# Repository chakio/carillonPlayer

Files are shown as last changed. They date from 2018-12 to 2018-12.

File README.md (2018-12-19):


carillonPlayer
====
* arduinoで鉄琴演奏ロボット  
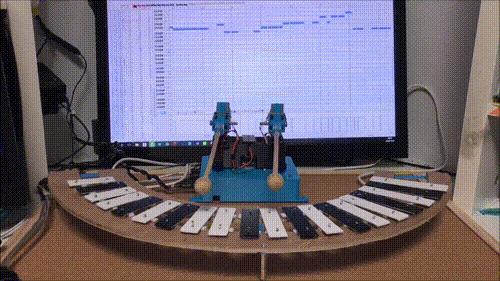
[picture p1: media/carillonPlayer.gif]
 
## Description
音データの可視化の一つとして、鉄琴演奏ロボットを作成しました。  
自作の円弧状に並ぶ鉄琴をサーボモータとソレノイドを駆使して演奏します。  
音付きの映像は[youtube](https://www.youtube.com/watch?v=UpVMlNcHM6o&feature=em-share_video_user)に公開しています。  
製作時期 2016年10月下旬〜12月初旬
## Composition
* マイコン: arduino mega
* ソレノイド: [タカハ機工株式会社 CB1037](http://www.takaha.co.jp/SHOP/cb1037.html)×2
* サーボモータ（腕,腰）:[GWSサーボ　S03T](http://akizukidenshi.com/catalog/g/gM-01794/)×3
* MIDI_Serial変換:[類似品](https://www.switch-science.com/catalog/2492/)

## Detail
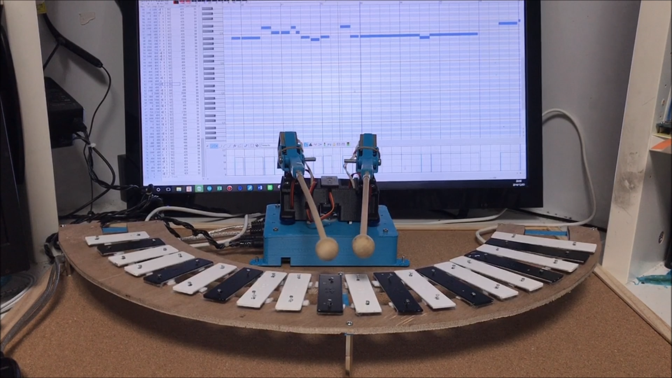
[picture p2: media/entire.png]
  

* Hardware  

鉄琴を叩く際、重要となるのは叩く際のスナップです。  
叩いた後にすぐに鉄琴からバチを離さないと、響かなくなってしまうためです。  
制作当初、すべてのアクチュエータにサーボモータを使用することを考えていました。  
しかし、プロトタイプの中で、サーボモータでスナップを効かせることは非常に困難であることがわかり、代わりのアクチュエータとしてソレノイドを採用しました。  
ソレノイドは非常に応答性がよく、一瞬だけ鉄琴を叩くという動作に適しているためです。   
以下の画像が、腕部分に着目した画像です。 

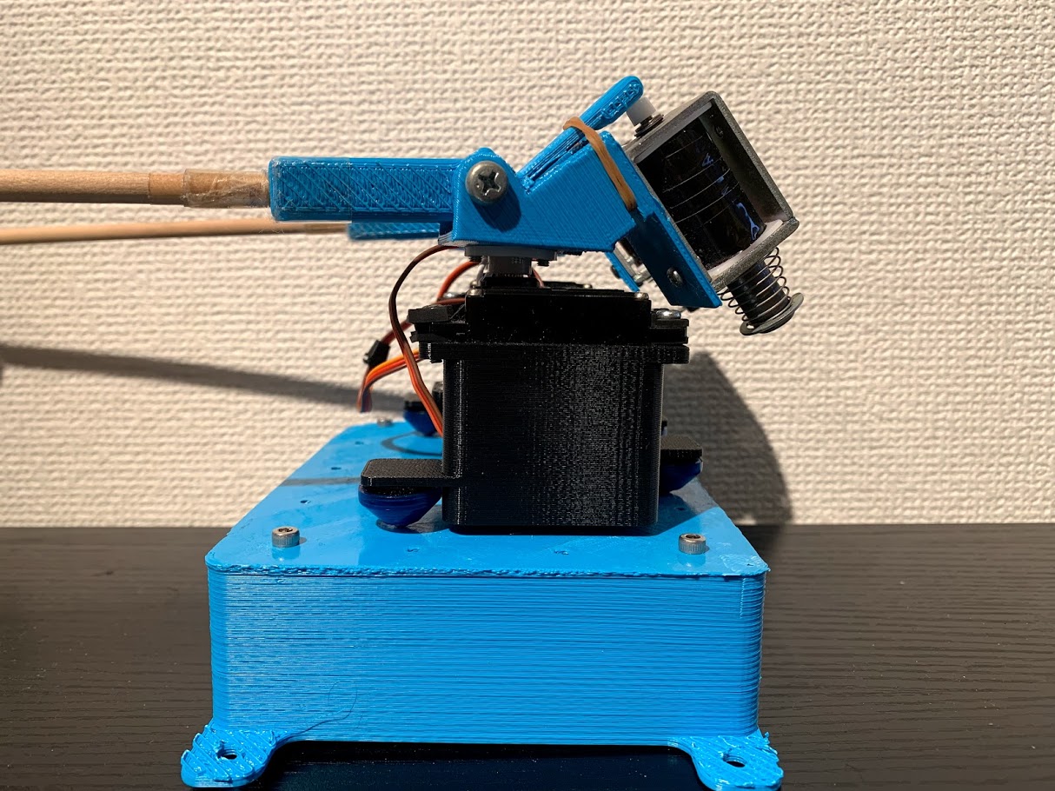
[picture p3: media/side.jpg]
  

腕部分は２つのパーツから構成されています。  
[１つ目](https://github.com/chakio/carillonPlayer/blob/master/model/solenoidHolder.stl)は、サーボモータにソレノイドを固定するパーツです。  
[２つ目](https://github.com/chakio/carillonPlayer/blob/master/model/stickHolder.stl)は、バチを把持するパーツです。  
これらを太めのネジで固定することで、ソレノイドの直動の力を回転に変換しています。  
また、一度下がったバチを元の位置に戻すために、輪ゴムを使用しています。  
このセットを２つ用意し、人と同じように双腕で演奏を行います。  
最後に、これらのパーツを[腰パーツ](https://github.com/chakio/carillonPlayer/blob/master/model/servoHolder.stl)に固定します。  

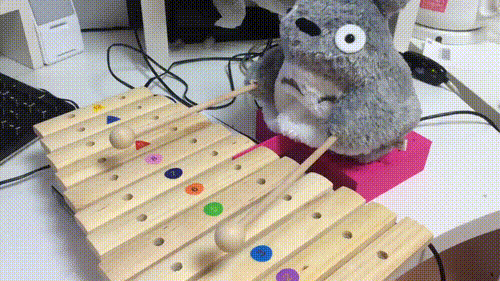
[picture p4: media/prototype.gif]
  

上記動画は、これまで説明した腕部分を使用し制作したプロトタイプのモデルです。  
小さな動きでリズミカルに叩く姿は愛らしいのですが、腕の速度に制限があり、演奏できる曲に制限がありました。  
そこで、サーボ自身を良い物に変えるのではなく、人と同様に腰部分に自由度を追加することで、遅い腕の動きを補うことを考えました。

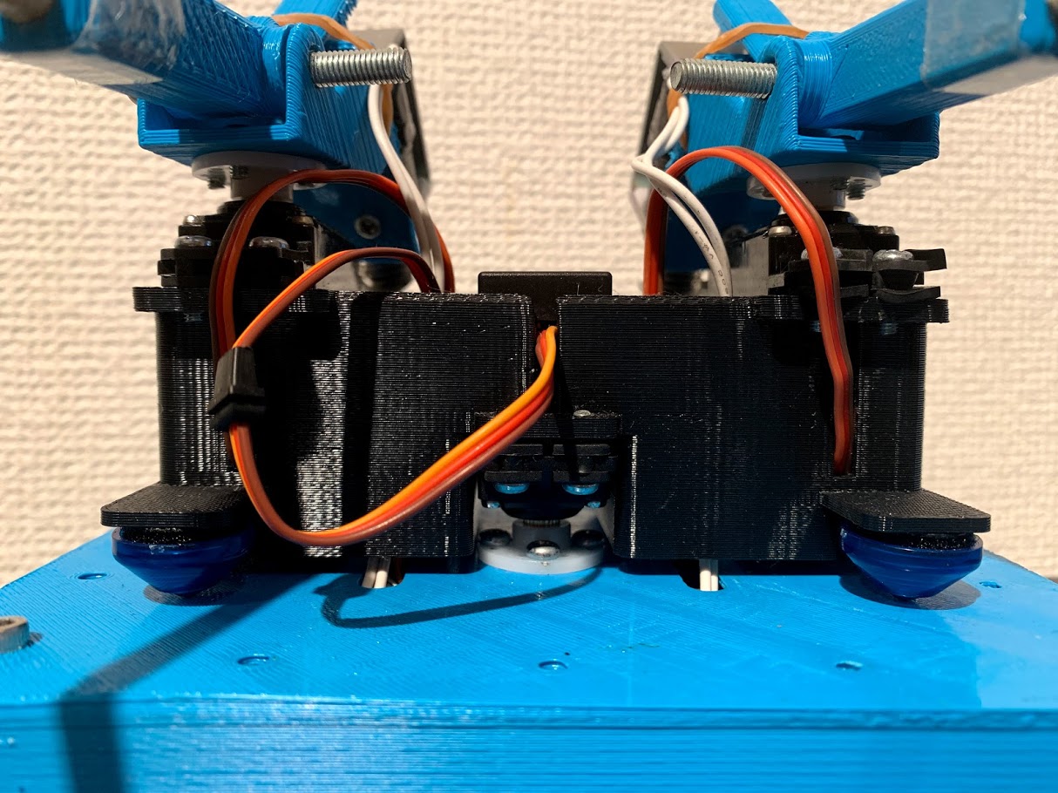
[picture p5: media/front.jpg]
  

２つの腕を固定する腰パーツに、もうひとつサーボモータを格納できるよう改良しました。   
回転をスムーズにすることと、サーボモータが痛むことを避けることを目的に４つのボールキャスターで支えるにしています。  
一番下の箱には回路などが格納されています。

* Carillon

本制作で最も苦労したのは、鉄琴周りと炒っても過言ではありません。  
まず、多くの音を演奏可能とするために、鉄琴の配置をこだわりました。  
一般的な鉄琴同様に、2列にすることを考えましたが、ハードウエアをより簡素にすることを優先し、すべての音を横に並べることを採用しました。  
更に、ロボットの可動範囲を考慮すると横一直線よりも、円弧状に配置されているほうが可動範囲をより有効活用できるため。鉄琴のプレートを円弧状に並べることとしました。  
プレートが円弧状に並ぶ鉄琴は一般的には入手できないため、入手可能な鉄琴を分解し、円弧状に再配置を行いました。  

次に、プレートの固定方法が非常に重要です。  
ただ板の上に固定するだけでは、全く音が響かなくなってしまいます。  
そこで、以下の２つの工夫を施しました。  
１つ目は、プレートをリジットな状態ではなくフローティングな状態で固定するために、プレートと板の間にフェルト生地をできるだけ細く入れています。  
接地面積が大きくなると音が響かなくなってしまいます。  
２つめは、プレートの板を一枚の板ではなく、板の内側を切り抜く加工を施しました。  
これにより、振動する空気の量がが増大し、比較的大音量かつ響くように改善されました。  

* Circuit

回路については以下の写真のとおりです。

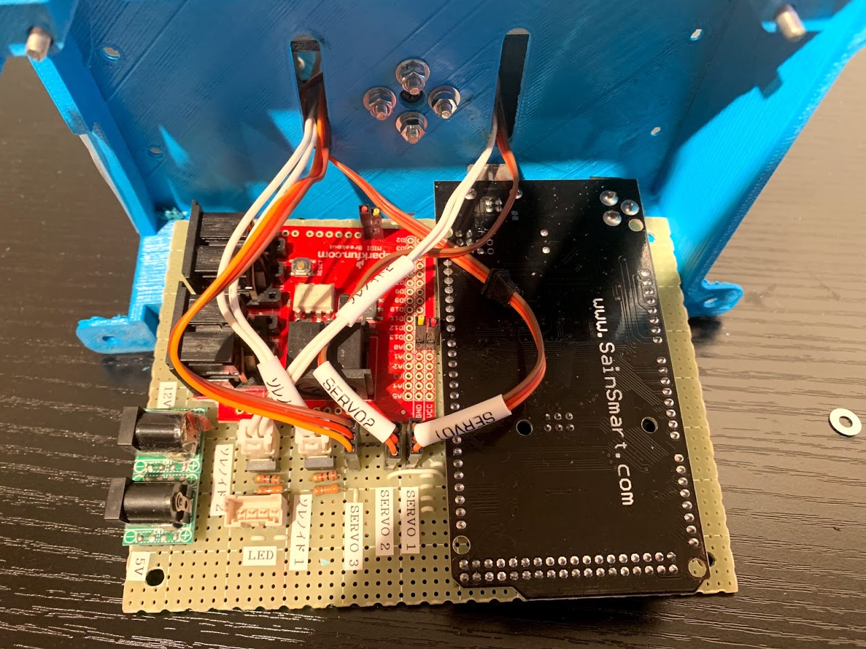
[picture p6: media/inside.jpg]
  

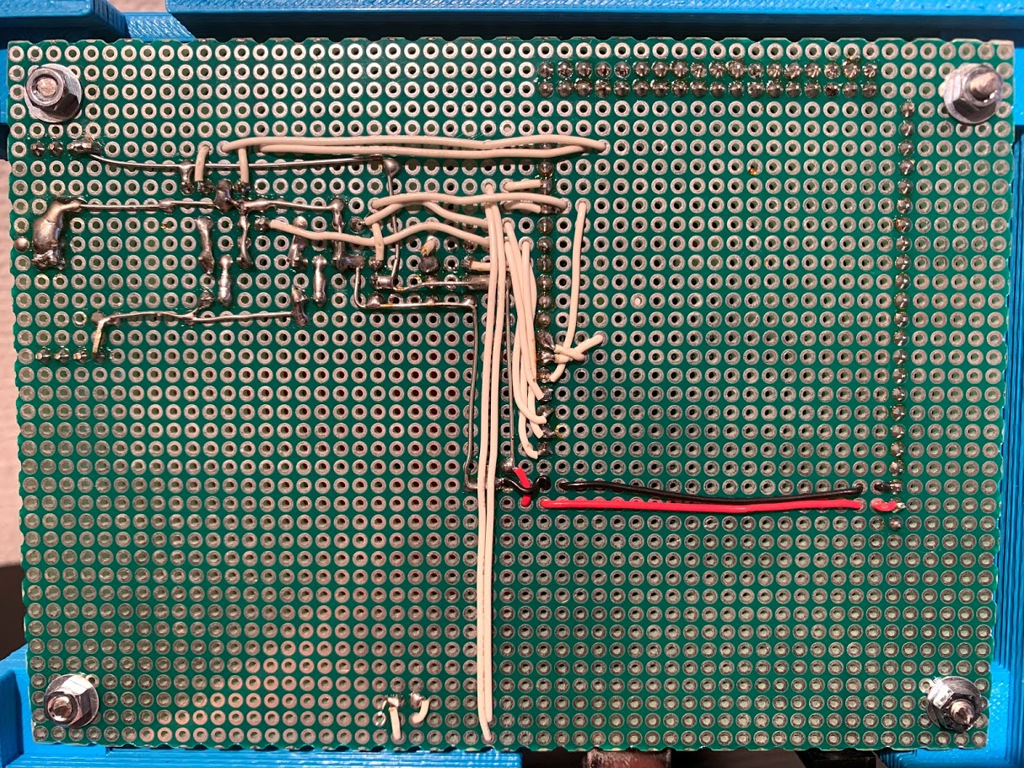
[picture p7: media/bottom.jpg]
 

arduino、サーボモータ用とソレノイド用にそれぞれ別電源を用意しています。  
また、ソレノイドはトランジスタで制御しています。  
ユニバーサル基板に手半田で作成しています。  
（arduinoは安価な互換機を使用しています）

* Program

プログラムの方では、それぞれの音に対しいくつかの腕と腰の姿勢セットを予め割り当てておきその中で最短時間で叩くことが可能な姿勢で叩くような仕組みになっています。  
さらなる性能向上には、予めMIDIデータを読み込み、書く時間に対する最適な姿勢を計画するような最適化問題を解く枠組みが必要だと考えています。

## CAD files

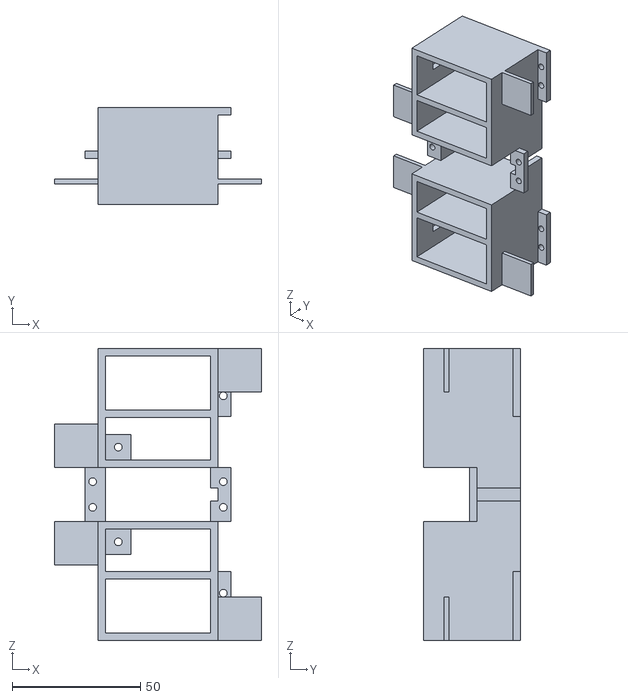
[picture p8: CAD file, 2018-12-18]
model/servoHolder.stl
81.0 x 38.0 x 114.0

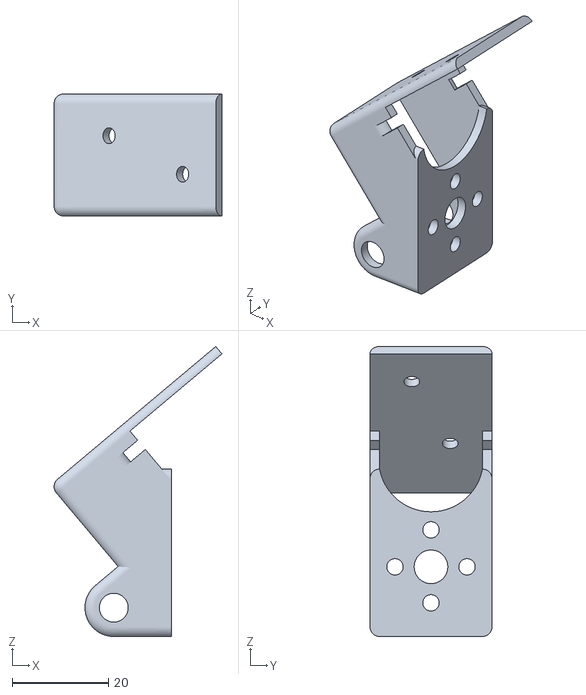
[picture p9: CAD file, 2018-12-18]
model/solenoidHolder.stl
34.9 x 25.4 x 60.4

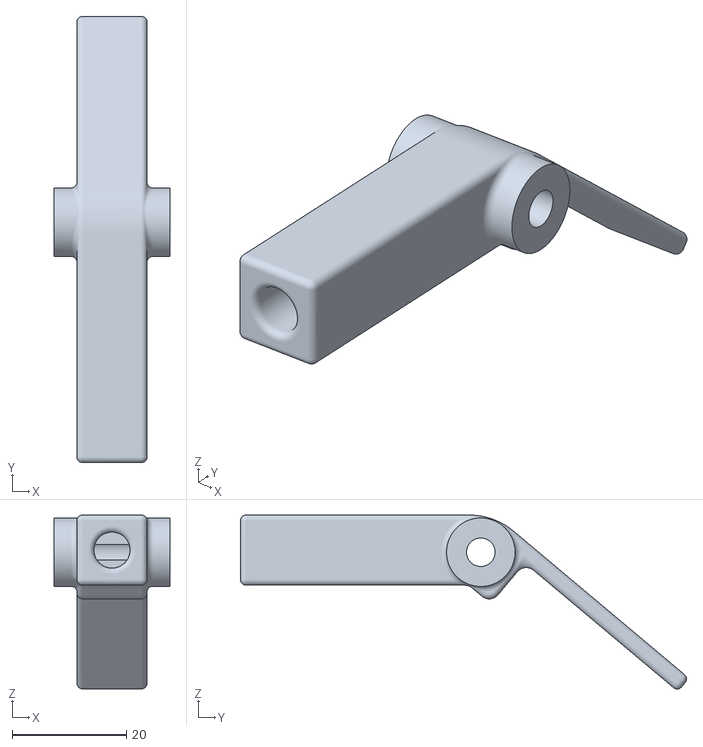
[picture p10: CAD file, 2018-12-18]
model/stickHolder.stl
20.3 x 78.1 x 30.5

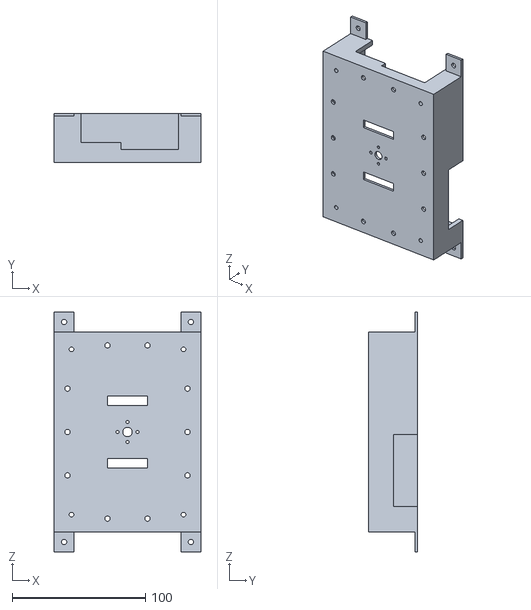
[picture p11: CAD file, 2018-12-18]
model/box.stl
110.0 x 37.0 x 180.0

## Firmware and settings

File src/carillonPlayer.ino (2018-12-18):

#include <Servo.h>
#include <MIDI.h>
#include "Ws2822s.h"
#define NUM_PIXELS 10 // 使用するWS2822Sの数
#define LED_PIN 2 // WS2822SのDAIピンにつなげるArduinoのピン番号
#define ADR_PIN 1

#define sorenoidLeft 4
#define sorenoidRight 5
Ws2822s LED(LED_PIN, NUM_PIXELS);
Servo servoLeft;
Servo servoRight;
Servo servoCenter;
int sound = 0;
// MIDIからToneに変換-------------------------------------
int  m2t[127] = {
0,0,0,0,0,0,0,0,0,0,
0,0,0,0,0,0,0,0,0,0,
0,0,0,0,0,0,0,0,0,0,
0,0,0,0,0,0,0,0,0,0,
0,0,0,0,0,0,0,0,1,2,
3,4,5,6,7,8,9,10,11,12,
13,14,15,16,17,18,19,20,0,0,
0,0,0,0,0,0,0,0,0,0,
0,0,0,0,0,0,0,0,0,0,
0,0,0,0,0,0,0,0,0,0,
0,0,0,0,0,0,0,0,0,0,
0,0,0,0,0,0,0,0,0,0,
0,0,0,0,0,0,0};

int targets[20][3][3];//どの音、センターの角度、手とセンター
int history[3];
int candidate[6];
int mini;
int minitarget;
int changeFlag=0;
MIDI_CREATE_INSTANCE(HardwareSerial, Serial1, midi1);

double servoArgLeft;
double servoArgRight;
double servoArgCenter;
double l1 = 20;
double l2 = 220;
double d1,d2;


void setup() 
{
  for(int i=0;i<20;i++)
  {
    for(int j=0;j<3;j++)
    {
      for(int k=0;k<3;k++)
      {
        targets[i][j][k]=0;
      }
    }
  }
  //座標設定
  for(int i=0;i<12;i++)
  {
    targets[i][0][1]=115;
    targets[i+4][1][1]=89;
    targets[i+8][2][1]=65;
  }
  targets[0][0][0]=115;
  targets[1][0][0]=109;
  targets[2][0][0]=102;
  targets[3][0][0]=96;
  targets[4][0][0]=91;
  targets[5][0][0]=85;
  targets[6][0][2]=102;
  targets[7][0][2]=97;
  targets[8][0][2]=91;
  targets[9][0][2]=85;
  targets[10][0][2]=79;
  targets[11][0][2]=72;

  targets[4][1][0]=116;
  targets[5][1][0]=110;
  targets[6][1][0]=104;
  targets[7][1][0]=98;
  targets[8][1][0]=92;
  targets[9][1][0]=86;
  targets[10][1][2]=101;
  targets[11][1][2]=96;
  targets[12][1][2]=90;
  targets[13][1][2]=84;
  targets[14][1][2]=78;
  targets[15][1][2]=71;
  
  targets[8][2][0]=114;
  targets[9][2][0]=108;
  targets[10][2][0]=102;
  targets[11][2][0]=96;
  targets[12][2][0]=90;
  targets[13][2][0]=84;
  targets[14][2][2]=100;
  targets[15][2][2]=94;
  targets[16][2][2]=89;
  targets[17][2][2]=83;
  targets[18][2][2]=76;
  targets[19][2][2]=69;
  

  midi1.begin();
  Serial.begin(9600);
  pinMode(sorenoidLeft,OUTPUT);
  pinMode(sorenoidRight,OUTPUT);
  servoLeft.attach(6);
  servoRight.attach(7);
  servoCenter.attach(3);
  servoLeft.write(90);
  servoRight.write(90);
  servoCenter.write(88);
  for(int i=0;i<3;i++)
  {
    history[i]=90;
  }
}

void loop() {
  uint8_t code;
  uint8_t ch,data1,data2;
  ch = 1;   //Read channel set;
  if (midi1.read()) {
    midi1.setInputChannel(ch);  // Channel
    switch(midi1.getType()) {
      case midi::NoteOn:
        data1 = midi1.getData1();    // note no
        if(m2t[data1]!=0)
        {
         changeFlag = 1;
         sound = m2t[data1]-1;
        }      
        break;
      default:
        break;
    }                     
  }
 
  if(changeFlag==1)
  {
    //候補挙げ
    for(int i=0;i<3;i++)
    {
      for(int j=0;j<2;j++)
      {
        if(targets[sound][i][j] !=0 && targets[sound][i][j+1] !=0)
        {
          if(j==1)
          {
            candidate[2*i+j]=max(abs(targets[sound][i][j]-history[j])*1,abs(targets[sound][i][j+1]-history[j+1]));
          }
          else
          {
            candidate[2*i+j]=max(abs(targets[sound][i][j]-history[j]),abs(targets[sound][i][j+1]-history[j+1])*1);
          }
        }
        else
        {
          candidate[2*i+j]=360;
        }
      }  
    }

    //最小値のターゲット見つける
    mini=400;
    minitarget=0;
    for(int i=0;i<6;i++)
    {
      if(candidate[i]<=mini)
      {
        minitarget=i;
        mini=candidate[i];
      }
    }
  
    //サーボ移動
    if(minitarget%2==0)//左手
    {
     servoLeft.write(targets[sound][(int)minitarget/2][0]);
     servoCenter.write(targets[sound][(int)minitarget/2][1]);
     delay(100);
     history[0]=targets[sound][(int)minitarget/2][0];
     history[1]=targets[sound][(int)minitarget/2][1];
     digitalWrite(sorenoidLeft,HIGH);
     delay(30);
     digitalWrite(sorenoidLeft,LOW);
    }
    else//右手
    {
      servoRight.write(targets[sound][(int)minitarget/2][2]);
      servoCenter.write(targets[sound][(int)minitarget/2][1]);
      delay(100);
      history[2]=targets[sound][(int)minitarget/2][2];
      history[1]=targets[sound][(int)minitarget/2][1];
      digitalWrite(sorenoidRight,HIGH);
      delay(30);
      digitalWrite(sorenoidRight,LOW);
    }
    changeFlag=0;
  }
}

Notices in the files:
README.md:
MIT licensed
